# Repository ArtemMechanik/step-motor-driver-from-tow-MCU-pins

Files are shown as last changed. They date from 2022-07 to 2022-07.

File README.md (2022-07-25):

# Драйвер шагового двигателя, управляемый двумя пинами микроконтроллера
Управление двумя H-мостами на транзисторах, используя два пина микроконтроллера с тремя состояниями.

Проблема: 
1. Необходимость использовать дешёвый драйвер для управления миниатюрным биполярным шаговым двигателем (альтернатива микросхеме STSPIN220).
2. Необходимость до минимума сократить количество пинов микроконтроллера, необходимых для управления двигателем, при этом, должна сохраниться возможность реализовывать волновой, полношаговый и полушаговый режимы управления двигателем.
3. Оптимизация отношения цена/функциональность.

Решение: каждый пин порта микроконтроллера (в данном случае микроконтроллер AVR) может находится в одном из трёх состояний: подтянут к плюсу питания, подтянут к минусу питания, находится в высокоимпедансном (HZ) состоянии. Три состояния теоретически позволяет контроллировать Н-мост, осущесвтляющий коммутацию обмотки двигателя: ток течёт в одну сторону, ток течёт в другую сторону (смена полярности напряжения), ток равен нулю. Используя два Н-моста для управления двумя обмотками биполярного шагового двигателя возможно реализовать простой драйвер, управляемый двумя пинами микроконтроллера.

Задача: разработать схему, осуществляющую преобразование трёх состояний пина микроконтроллера в сигналы, пригодные для управления Н-мостом.

В качестве микроконтроллера был выбран ATtiny13A в корпусе DFN10. Для управления шаговым двигателем используется две кнопки. При нажатии на одну кнопку, двигатель вращается влево, при нажатии на другую кнопку - вправо. Количесвто шагов определяется программой. Скорость вращения не изменяется и задаётся программно.

Разработана отладочная плата. Схема обвязки микроконтроллера:
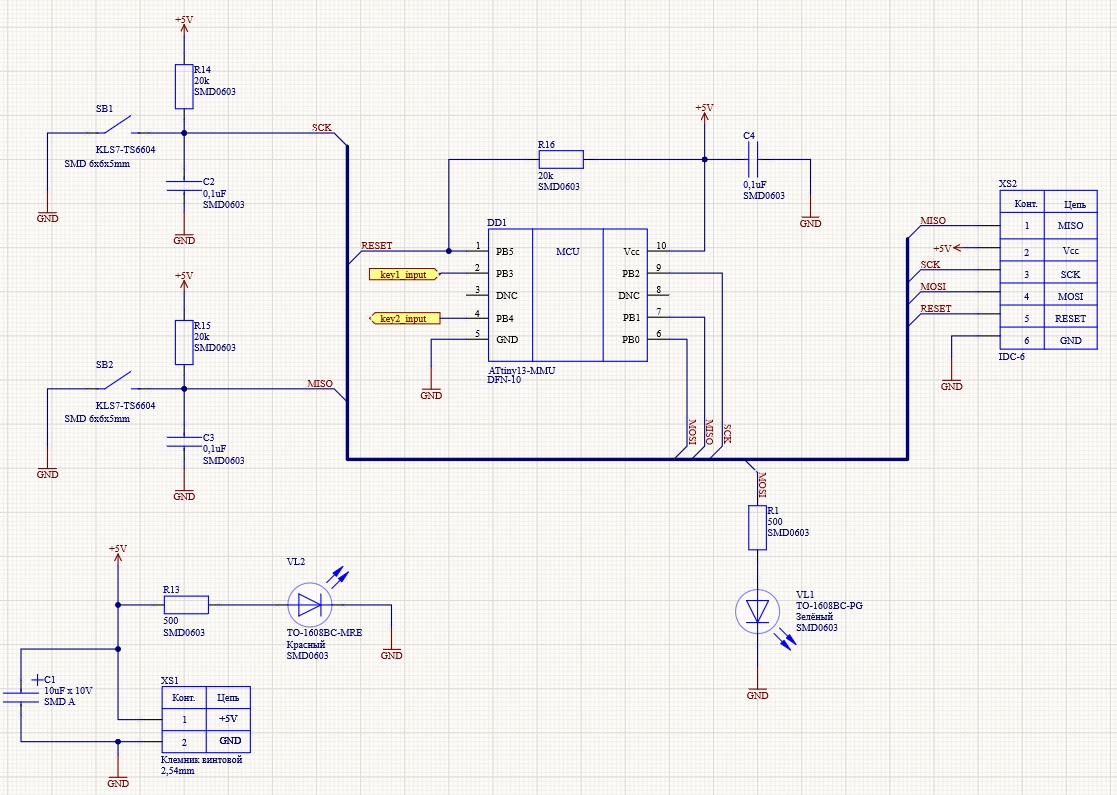
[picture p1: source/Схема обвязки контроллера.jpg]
Схема обвязки контроллера


Предложена следующая схема работы переключателя.Схема является коммутатором, вход подключается к пину микроконтроллера. По умолчанию выходы out1 и out2 подтянуты к питанию. Пин микроконтроллера может иметь три состояния:
1. Конфигурация на выход. Подтянут к питанию. В этом случае out2 прижимается к земле.
2. Конфигурация на выход. Подтянут к земле. В этом случае out1 прижимается к земле. 
3. Конфигурация на вход (HZ). В этом случае out1 и out2 остаются подтянутыми к питанию.
Входные транзисторы с общей базой образуют пару компараторов. Напряжение на базах равно половине напряжения питания. Напряжение на эммитерах не отличается от напряжения базы больше чем на 0.6В, поэтому транзисторы закрыты. Как только появляет перекос напряжения на эммитерах, отдин из транзисторов открывается.

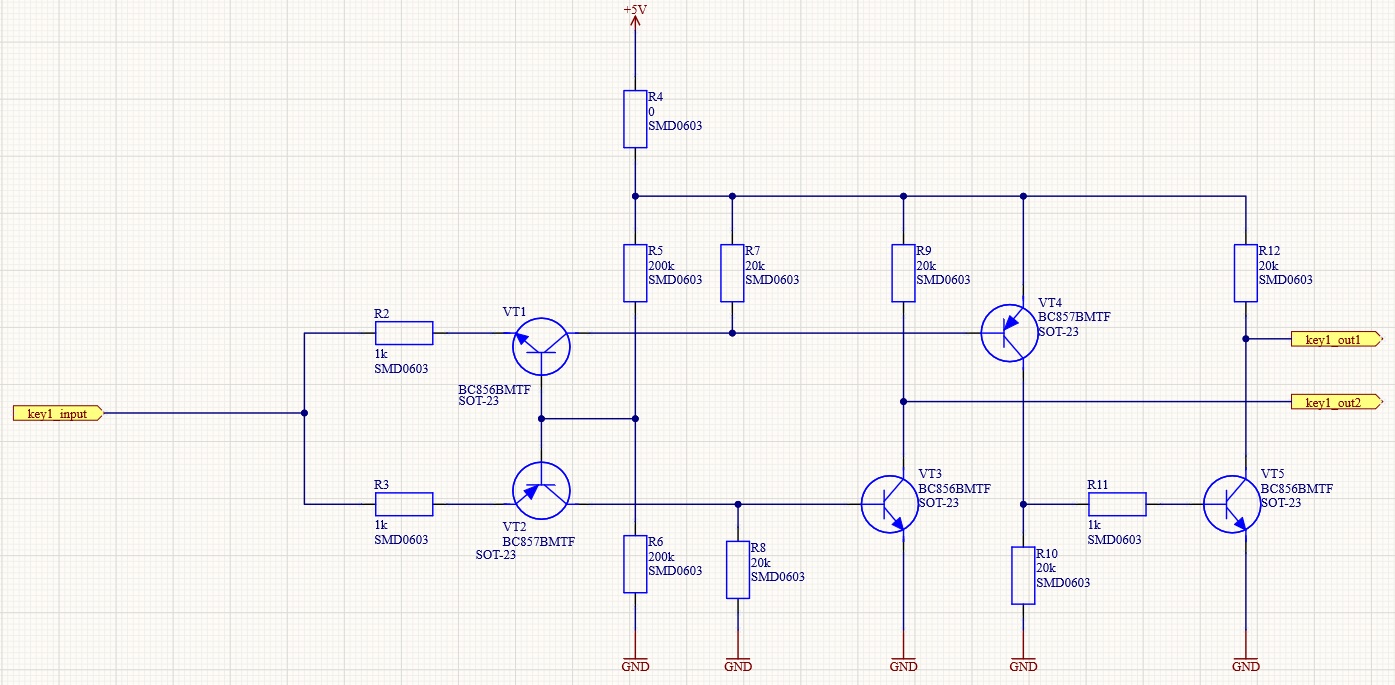
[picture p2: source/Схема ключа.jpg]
Схема ключа


Произведено моделирование работы ключа на биполярных транзисторах в Multisim 14.1. Результаты моделирования показали работоспособность концепции.
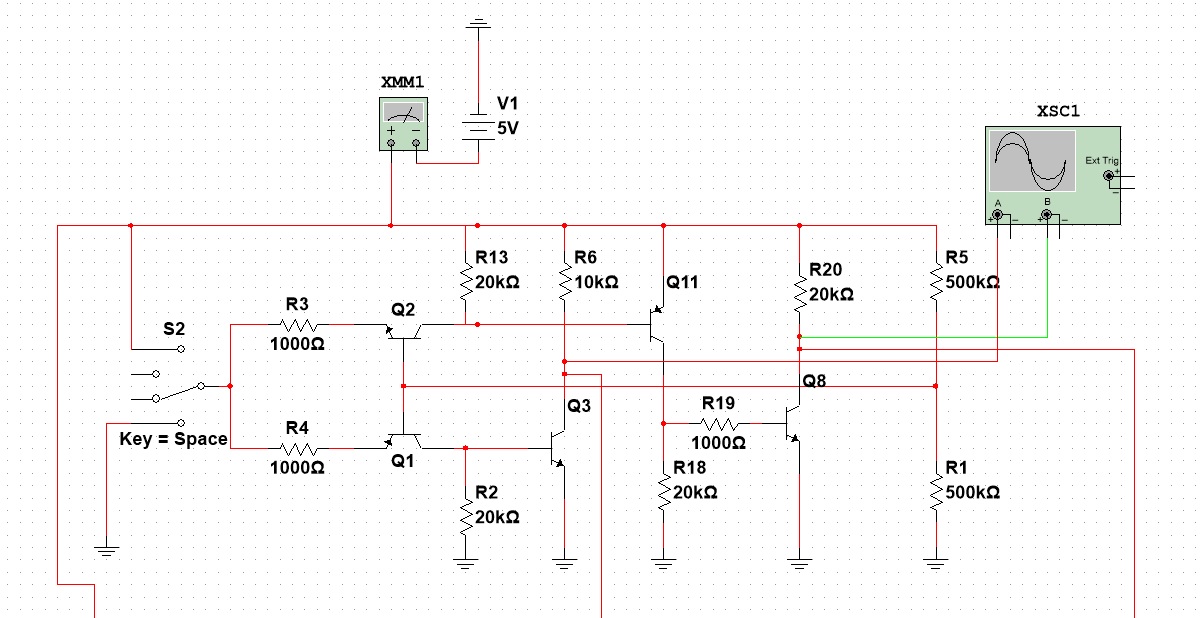
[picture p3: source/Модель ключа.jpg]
Моделирование ключа


Для коммутации обмотки шагового двигателя была выбрана схема классического Н-моста. Никаких схемотехнических решений по организации зажержек при переключении направления тока в нагрузке (deadtime) не предусмотрена. Организация deadtime осуществляется программно.
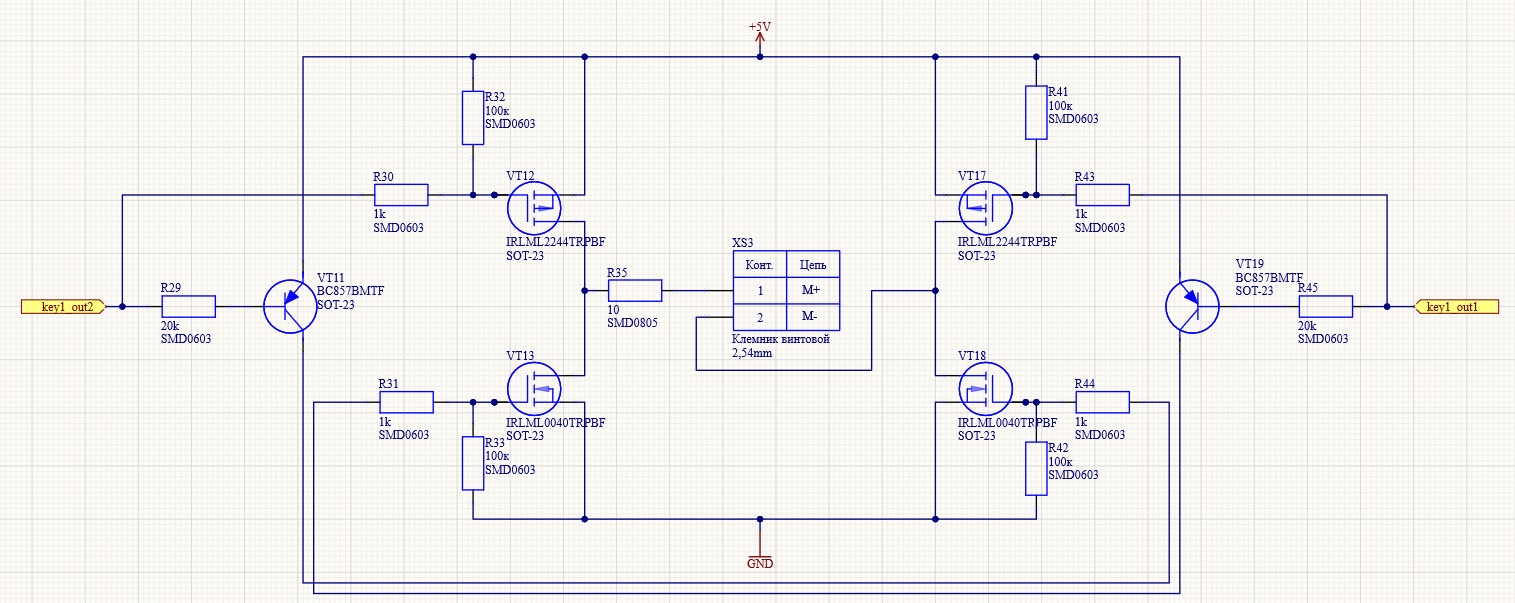
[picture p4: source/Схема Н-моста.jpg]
Схема Н-моста


Топология печатной платы Altium Designer:
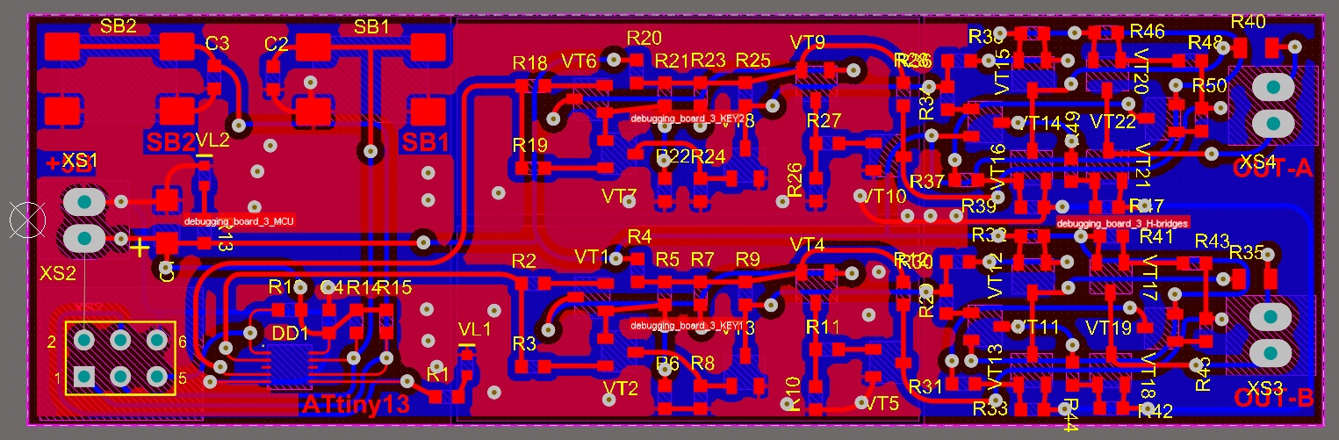
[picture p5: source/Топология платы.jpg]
Топология платы


3D модель печатной платы Altium Designer:
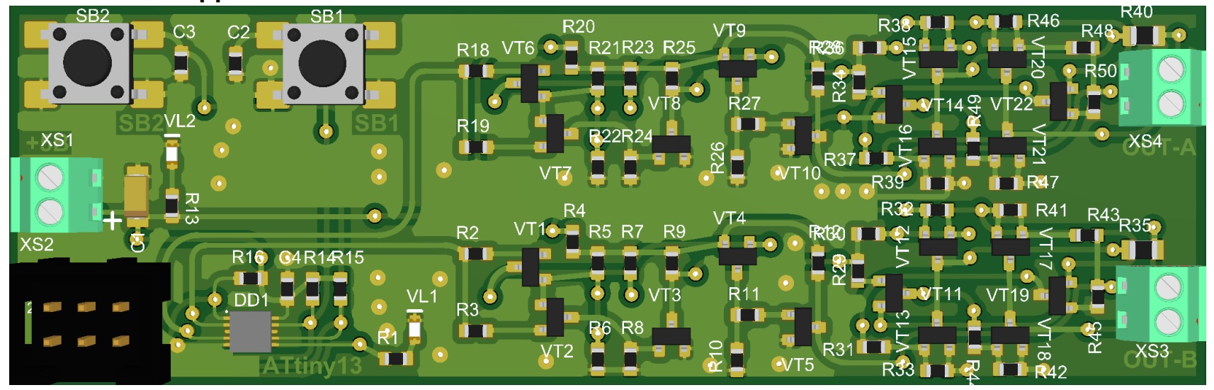
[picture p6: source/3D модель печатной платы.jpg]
3D модель печатной платы


Отладочная плата изготовлена по технологии ЛУТ:
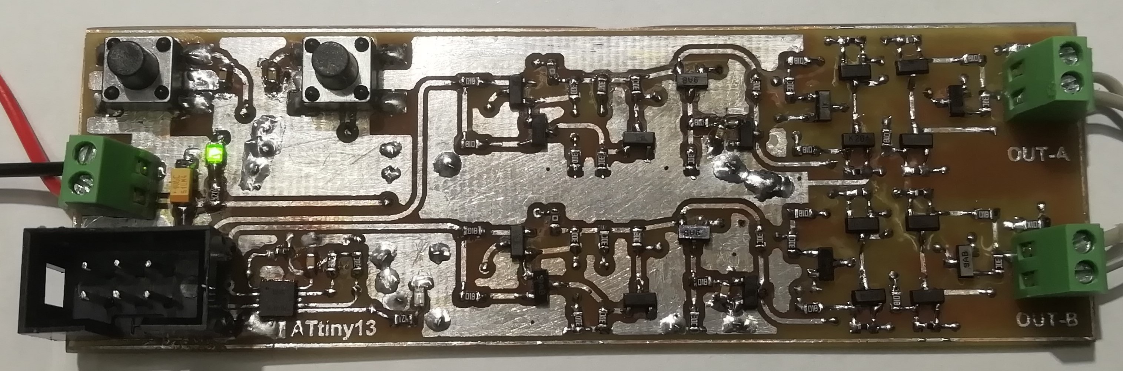
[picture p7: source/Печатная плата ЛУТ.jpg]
отладочная плата ЛУТ


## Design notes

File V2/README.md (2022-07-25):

Версия драйвера шагового двигателя, выполненная на полевых транзисторах.
Использование полевых транзисторов позволило снизить ток утечки, образуемый делителем напряжения в цепи базы (затвора) входных транзисторах коммутатора.
Удалось снизить общее количество транзисторов в схеме.
Разработана принципиальная схема устройства. Проведено моделирование работы коммутатора и Н-моста. Моделирование показало, что предложенная схема реализует необходимый функционал.

Принципиальная схема коммутатора на полевых транзисторах:
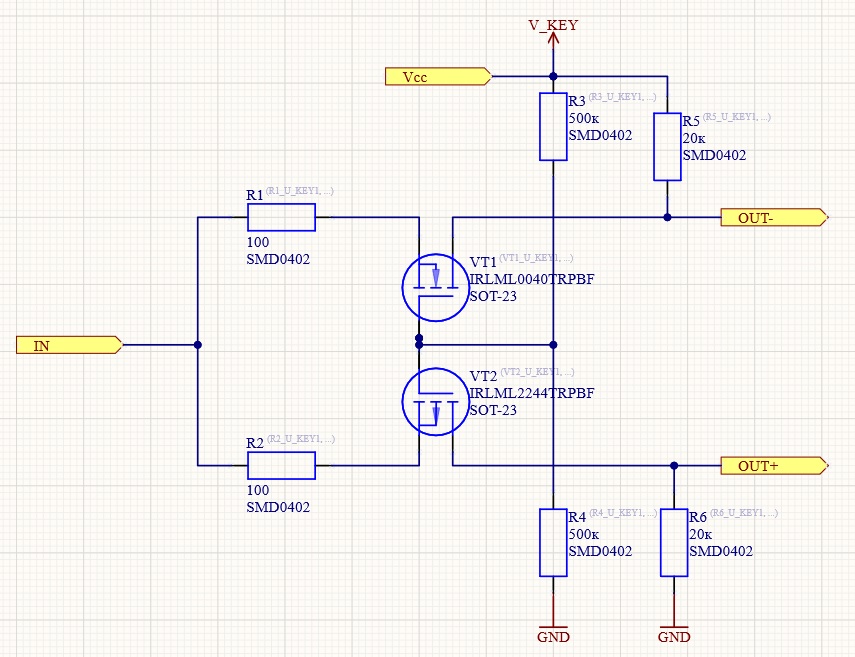
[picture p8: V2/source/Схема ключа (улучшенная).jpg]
Схема ключа улучшенная


Модель коммутатора в Multisim 14.1:

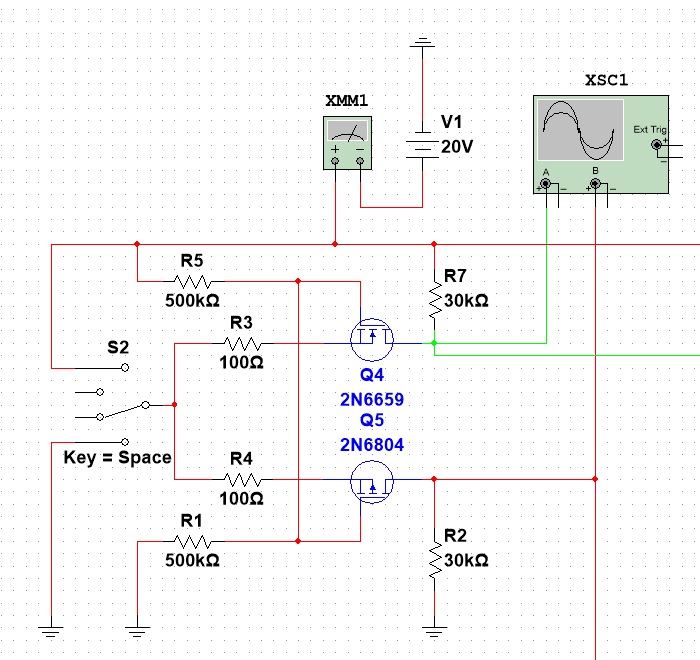
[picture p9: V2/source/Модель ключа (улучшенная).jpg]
Схема ключа улучшенная


Схема Н-моста на полевых транзисторах:
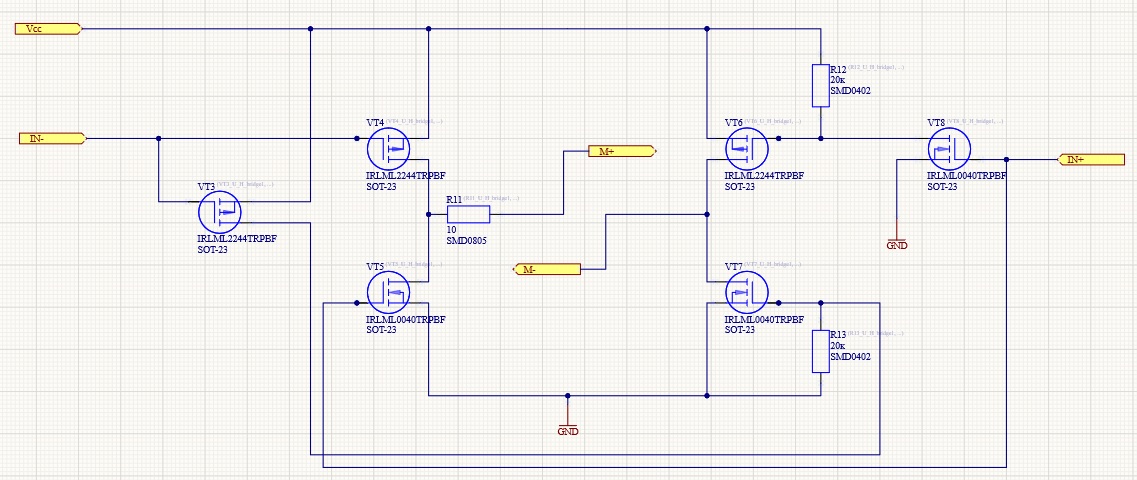
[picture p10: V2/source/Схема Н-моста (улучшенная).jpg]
Схема ключа улучшенная


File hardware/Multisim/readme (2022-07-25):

Моделирование предложенной схемы в программе Multisim 14.1

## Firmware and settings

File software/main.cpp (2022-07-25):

/*
микроконтроллер ATtiny13A
тактовая частота 9,6 МГц
 */ 
#define F_CPU 9600000UL

#include <avr/io.h>
#include <util/delay.h>
#include <avr/interrupt.h>

//íàçíà÷åíèå âûâîäîâ
#define BUTTON1_PIN PB2
#define BUTTON2_PIN PB1
#define LED_PIN		PB0
#define KEY1_PIN	PB3
#define KEY2_PIN	PB4

#define LED_ON		PORTB |= (1<<LED_PIN)
#define LED_OFF		PORTB &=(~(1<<LED_PIN))

#define HZ		0
#define HIGH	1
#define LOW		2

#define FORWARD	0
#define BACK	1

#define DEADTIME	1000 //ìêÑ



void key1State (uint8_t state) {
	DDRB &=(~(1<<KEY1_PIN));
	PORTB &=(~(1<<KEY1_PIN));
	if(state == 1) {
		DDRB	|=(1<<KEY1_PIN);
		PORTB	|=(1<<KEY1_PIN);
	}
	else if(state == 2) {
		DDRB	|=(1<<KEY1_PIN);
		PORTB	&=(~(1<<KEY1_PIN));
	}
}

void key2State (uint8_t state) {
	DDRB &=(~(1<<KEY2_PIN));
	PORTB &=(~(1<<KEY2_PIN));
	if(state == 1) {
		DDRB	|=(1<<KEY2_PIN);
		PORTB	|=(1<<KEY2_PIN);
	}
	else if(state == 2) {
		DDRB	|=(1<<KEY2_PIN);
		PORTB	&=(~(1<<KEY2_PIN));
	}
}

void delayMs (unsigned int delay) {
	for(unsigned int i=0; i<delay; i++) {
		_delay_ms(1);
	}
}

void pinSetup() {
	DDRB = (1<<LED_PIN)|(0<<BUTTON1_PIN)|(0<<BUTTON2_PIN);
	PORTB |=(1<<BUTTON1_PIN)|(1<<BUTTON2_PIN);
	
	LED_OFF;
	key1State(HZ);
	key2State(HZ);
}

void motorStep (uint8_t direction, uint8_t step, uint16_t delay) {
	if(direction == FORWARD) {
		while(step > 0) {
			// обмотка A				// обмотка В
			key1State(HIGH);
			delayMs(delay/2);
								key2State(HZ);
								_delay_us(DEADTIME);
							
								key2State(HIGH);
								delayMs(delay/2);
		
			key1State(HZ);
			_delay_us(DEADTIME);
		
			key1State(LOW);
			delayMs(delay/2);
		
								key2State(HZ);
								_delay_us(DEADTIME);
							
								key2State(LOW);
								delayMs(delay/2);
		
			key1State(HZ);
			_delay_us(DEADTIME);
		
							
							
			
			step--;
		}
	}
	else if(direction == BACK) {
		while(step > 0) {
			// обмотка А				// обмотка В
			key2State(HIGH);
			delayMs(delay/2);
								key1State(HZ);
								_delay_us(DEADTIME);
			
								key1State(HIGH);
								delayMs(delay/2);
			
			key2State(HZ);
			_delay_us(DEADTIME);
			
			key2State(LOW);
			delayMs(delay/2);
			
								key1State(HZ);
								_delay_us(DEADTIME);
			
								key1State(LOW);
								delayMs(delay/2);
			
			key2State(HZ);
			_delay_us(DEADTIME);
			
			
			
			
			step--;
		}
	}
	_delay_ms(200);
}

int main(void) {
    pinSetup();
	
    while (1) {
		if(!(PINB&(1<<BUTTON1_PIN))) {
			LED_ON;
			//key1State(HIGH);
			motorStep(BACK,4,10);
		}
		else if(!(PINB&(1<<BUTTON2_PIN))) {
			LED_ON;
			//key1State(LOW);
			motorStep(FORWARD,4,10);
		}
		else {
			LED_OFF;
			key1State(HZ);
			key2State(HZ);
		}
    }
}
